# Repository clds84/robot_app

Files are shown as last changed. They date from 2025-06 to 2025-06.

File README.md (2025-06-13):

# Robot Project
<p align= "center" style="margin: 30px">
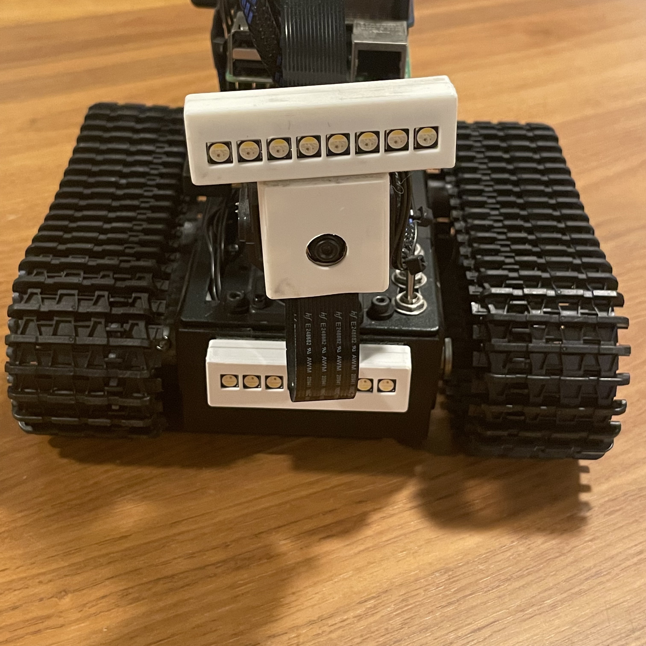
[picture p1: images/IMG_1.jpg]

</p>

This robot project is controlled via a client web interface served at `http://robot-hostname.local:8000` using WebSockets. Using a hostname instead of an IP address makes it easy to connect, even through a mobile hotspot, when configuring or troubleshooting WiFi in the field.

For my setup, the robot pairs with a dedicated **Mission Control** Pi that acts as a robot client app. It sends battery sensor readings (for its own display and the Pi) over sockets and opens the robot’s web interface in a browser for control via four rotary encoders and four key switches.

🔗 [Mission Control repo here](https://github.com/clds84/mission_control_app)

> A regular laptop or desktop can also be used as a client if you don’t want to build Mission Control hardware.

## 📑 Table of Contents

1. [Setup (Overview)](#-setup-overview)
2. [Features](#features)
3. [Hardware](#hardware)
4. [3D Printed Parts](#3d-printed-parts)
5. [How to Build](#how-to-build)
6. [System Overview](#system-overview)
7. [How to Use](#how-to-use)
8. [Dependencies](#-dependencies)
9. [Service Files](#service-files---copy-in-system-and-user-services)
10. [Powering On for Use](#powering-on-for-use)
11. [Operating robot in a new environment](#operating-robot-in-a-new-environment)
12. [Controls for Laptop or Desktop](#controls-for-laptop-or-desktop)
13. [Code](#code)
14. [Troubleshooting](#troubleshooting)

## 🔧 Setup (Overview)

This project involves physical hardware, system services, and network setup. Use this section as a high-level checklist to guide your deployment.

1. **Assemble hardware**  
  Wire up all components according to the parts list and included `.stl` files for 3D-printed mounts and protection.

2. **Flash Raspberry Pi OS and configure WiFi**  
  Set up the robot Pi headlessly using a mobile hotspot to enable SSH access and configure primary WiFi with `nmcli`.

3. **Clone this repo and set up the environment**
  ```bash
  git clone https://github.com/clds84/robot_app
  cd robot_app
  python3 -m venv venv
  source venv/bin/activate
  pip install -r requirements.txt
  ```
4. **Copy services**

    Copy `app.service, stream.service`, and `display_hat_stats.service` into `~/.config/systemd/user/` 
    Copy `neopixel.service` into `/etc/systemd/system/` (must run as root)
5. **Enable and start services**

    For user-level services:
    ```bash
    systemctl --user enable app.service stream.service display_hat_stats.service
    systemctl --user start app.service steam.service display_hat_stats.service
    ```
    For root-level service
    ```bash
    sudo systemctl enable neopixel.service
    sudo systemctl start neopixel.service
    ```
6. **Power on devices**

    Boot up both the robot Pi and the Mission Control Pi (if used).
7. **Access the robot interface**

    Open a browser and go to:
    `http://robot-hostname.local:8000`
8. **Operate the robot**

    Use key controls with a Mission Control, laptop, or desktop described below to drive motors, control motor speed, adjust servos, toggle LEDs and control brightness.

## Features

- WebSocket-based communication between robot and client
- Local web interface (`index.html`) served by the robot
- Integrated camera stream via `stream.py`
- Handles onboard logic for:
  - DC motors (4-wheel drive)
  - Pan/tilt servos for camera
  - NeoPixel LED sticks
- Emits battery sensor readings over sockets
- Receives sensor input (e.g., Mission Control battery levels) over sockets (if using Mission Control client)

## Hardware

- [Raspberry Pi 4]()
- [Adafruit DC Motor HAT]()
- [Adafruit Servo HAT]()
- [Pi Camera]()
- [Pan/tilt servo bracket]()
- [2 DC motors (one per side)]()
- [2 servo motors (for X and Y axes)]()
- [2 Adafruit NeoPixel sticks]()
- [2 Adafruit PowerBoost chargers (for Lithium Polymer (LiPo) battery)]()
- [2 Adafruit battery gauge monitors]()
- [Adafruit I2C multiplexer]()
- [Adafruit display HAT (for WiFi status and battery voltage)](https://www.adafruit.com/product/4393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)

## 3D Printed Parts

Included `.stl` files for:

- Camera housing  
- NeoPixel stick holders  
- Underbody chassis cover (motor protection)  

> **Note:** The underbody is a quick solution for protection. It can be a little tedious to remove/install but functional.

## How to Build

Please refer to the included photos for build guidance. Since chassis types may vary, I didn’t document the mechanical build step-by-step, but the photos will provide some insight. 

**Tips:**

- **Breadboard or loosely wire** all components first to test functionality before permanent mounting.
- Use a **jumper wire kit** and proper standoffs for organization and flexibility.
- You may need a **conical file** to widen mounting holes on the battery gauges or multiplexer to fit standoffs.
- The **display HAT** might seem redundant since battery data is also shown in the web interface, but it’s useful for checking battery level before/after shutdown, or confirming WiFi connection with a button press.
- **Power stacking**: The PowerBoost, battery gauges, and multiplexer stack cleanly using standoffs when aligned properly.

---

### Back Right 
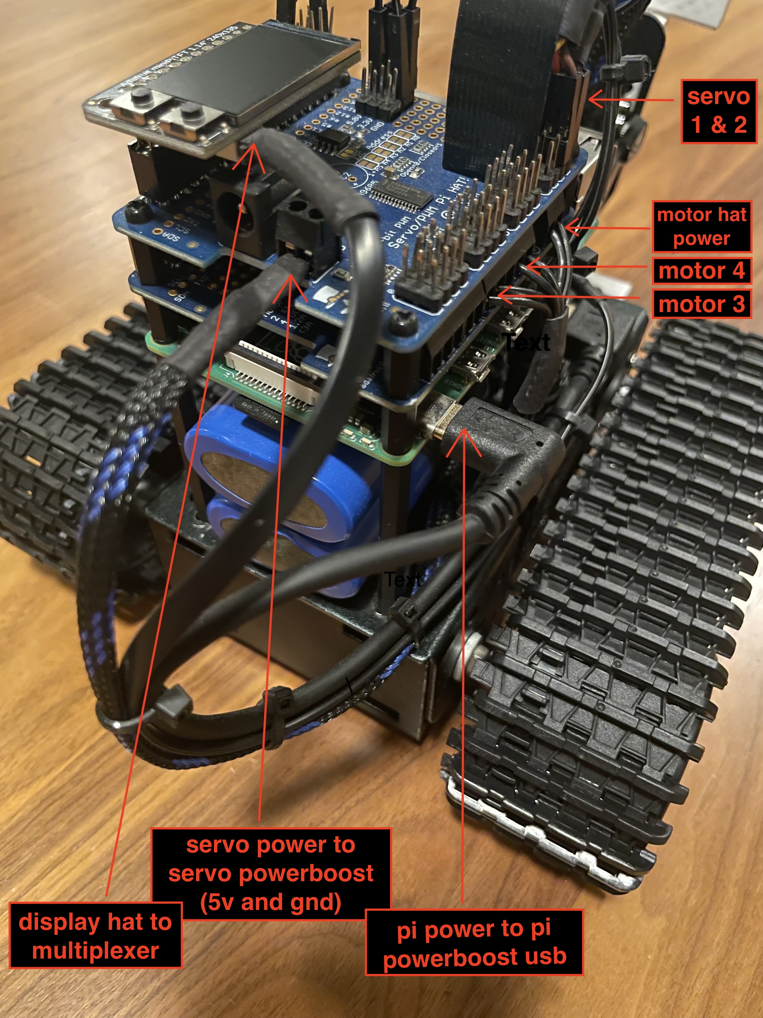
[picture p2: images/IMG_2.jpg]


This image shows the Display HAT stacked on the servo HAT, which is on top of the DC motor HAT, all mounted on the Raspberry Pi.  Other connection points for servo power, the display HAT, and the Pi power, are shown more clearly in later images. 

The six wires, two per DC motor, plus one for power and one for ground, run down straight down under the chassis. 

The **servo 1 & 2 wires** in the top right of the image come from the servo motors and are also shown more clearly in later images. The headers on this side of the servo HAT correspond to the 16-channel servo layout, and each row includes power, ground, and signal.

The camera ribbon runs through a slit in both the dc motor and servo HATs. 

---

### Multiplexer/Battery Gauge/Powerboost Stack
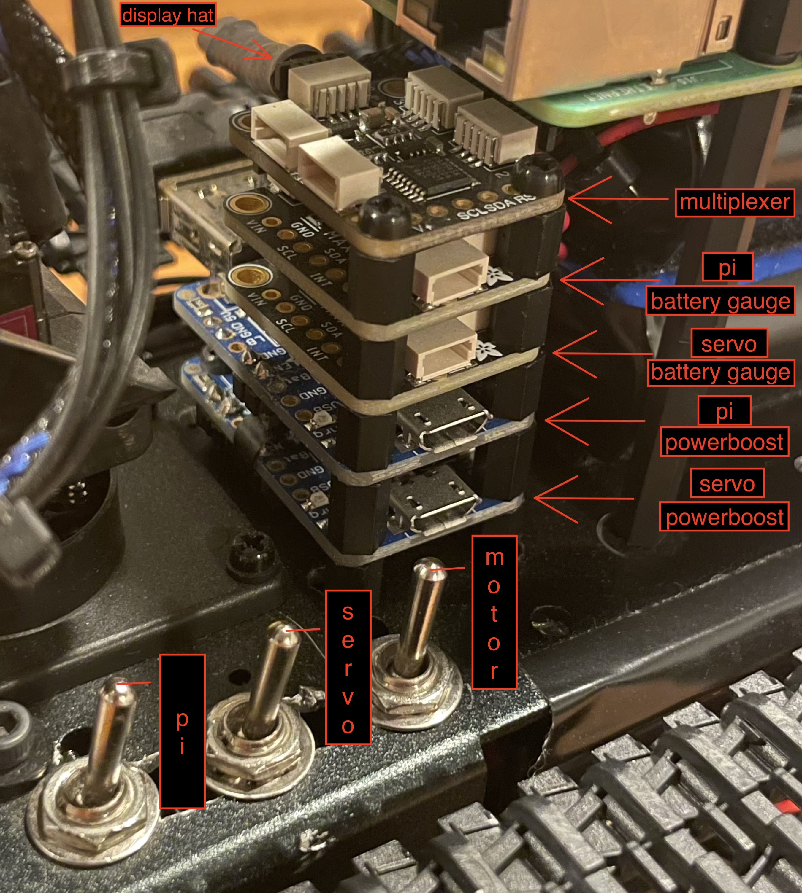
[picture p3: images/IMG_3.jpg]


This image shows:
  - Toggle switches for pi
  - Multiplexer
  - Battery gauges
  - Pi PowerBoost
  - Servo PowerBoost
  
  The power and ground wires for the DC motor ([motor wires](#back-right)) are connected to the motor toggle switch under the chassis. The toggle switches for the Pi and servo will be mentioned again.

---

### Top Left
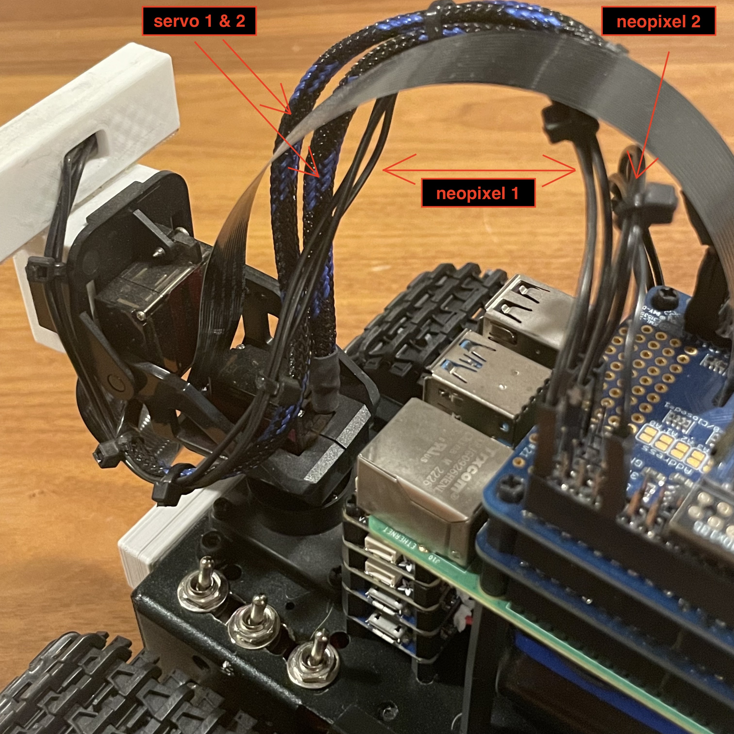
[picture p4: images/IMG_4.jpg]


The wires identified in this image are for:
  - NeoPixel 1 and 2 
  - Servo 1 and 2

Each Neopixel has a power, ground, and signal wire connected to the headesr on the servo HAT which correspond to the Pi's GPIO layout. The signal wire for NeoPixel 1 is connected to D21 and the one for NeoPixel 2 is connected to D12.

The wires for NeoPixel 2 will be mentioned again in a later image.

---
### Side View 
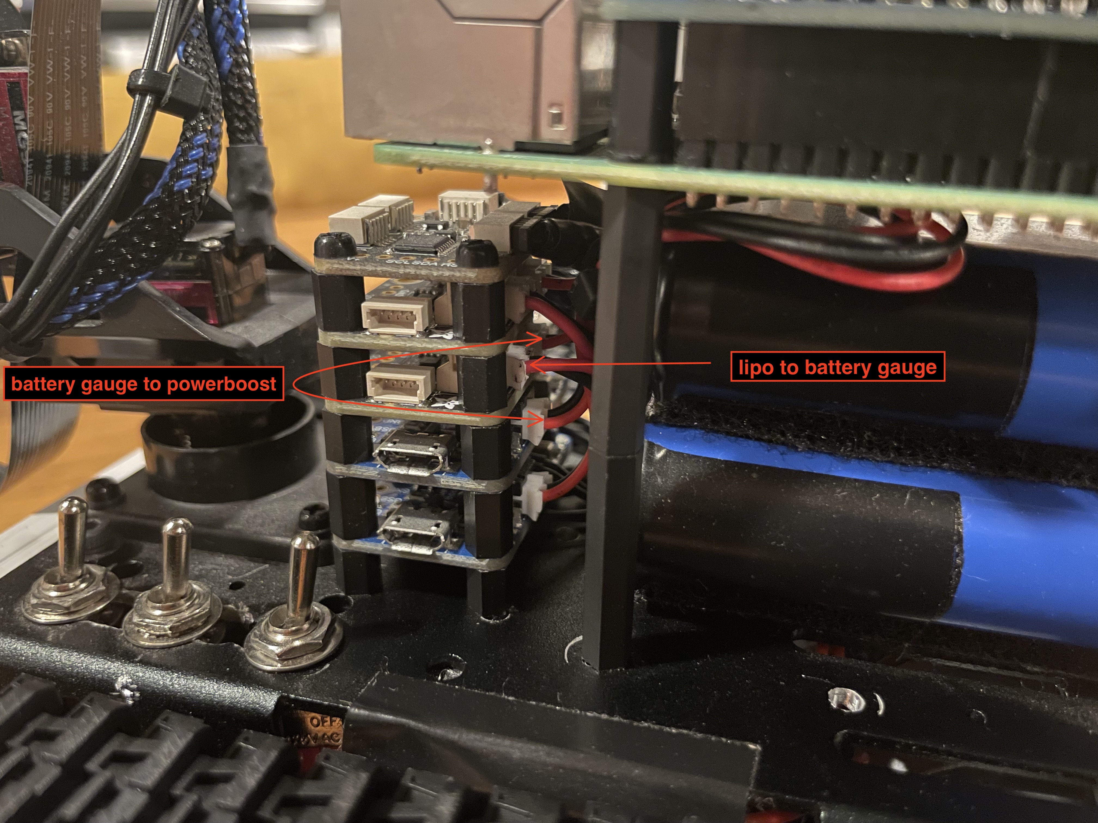
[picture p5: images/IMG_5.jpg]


Connect the LiPo JST connector to the battery gauge, then a JST cable from the battery gauge to the PowerBoost (these are the steps per battery gauge/PowerBoost combo).

---

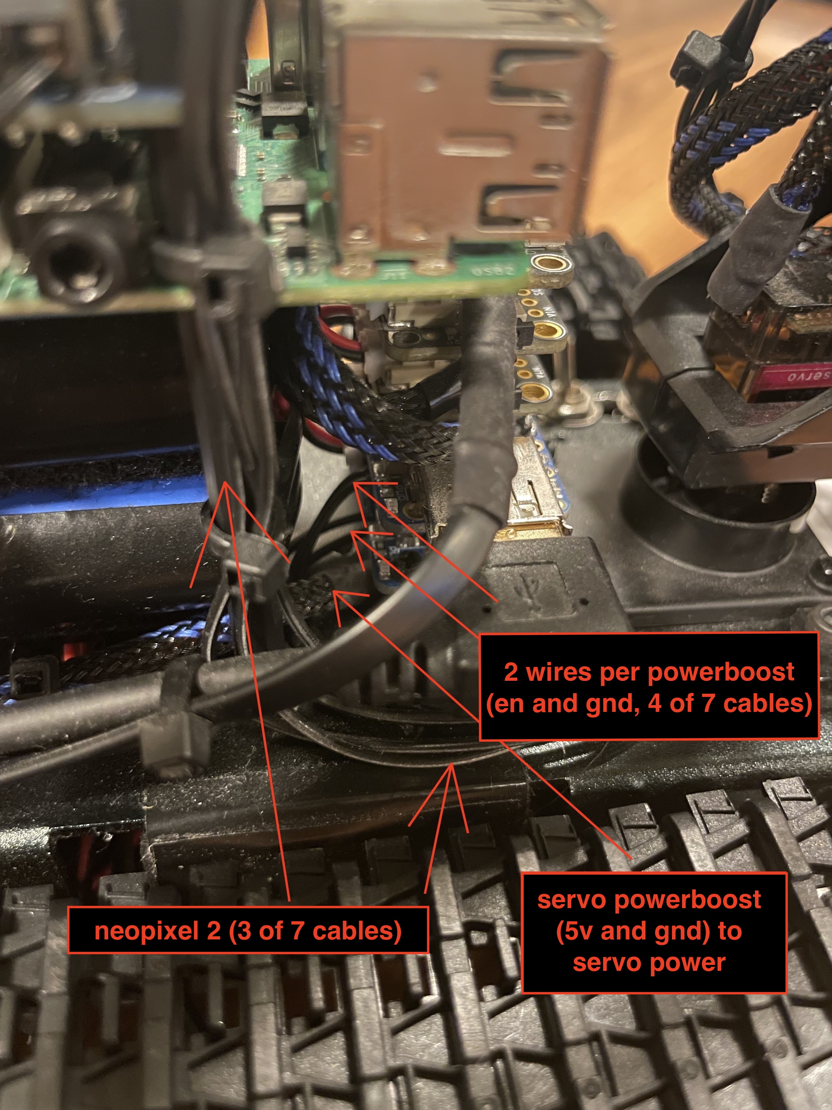
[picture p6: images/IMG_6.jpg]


Wires identified for:
  - Neopixel 2 [NeoPixel connection on HAT](#top-left)
  - Servo power ([Servo power](#back-right)) - use 5v and GND pins
  - PowerBoosts - use EN & GND pins

For aesthetic purposes, 90-degree headers are soldered to the bottom of each PowerBoost, facing inward toward the midline.

> **Note:** The EN and GND pins used for each PowerBoost (Pi and servo) run under the chassis and connect to the Pi and servo toggle switches. The difference between these and the motor switch is that the motor switch does not utilize a PowerBoost; instead, it enables power directly from the LiPo to the DC motor HAT, with no intermediary connections to be made. However, for the Pi and servo, the EN and GND will result in a LOW reading when the toggle switch is operated, and that will allow power from LiPo -> PowerBoost -> Pi/servo. The reason for doing this is to control the HIGH position when not using the robot and/or charging the LiPo batteries. If the toggle switch is in an OFF position, the PowerBoosts will not transfer voltage to the servo Hat or the Pi. However, the PowerBoosts will be operational for charging, via headers or the micro-usb port.

---

### Front Right
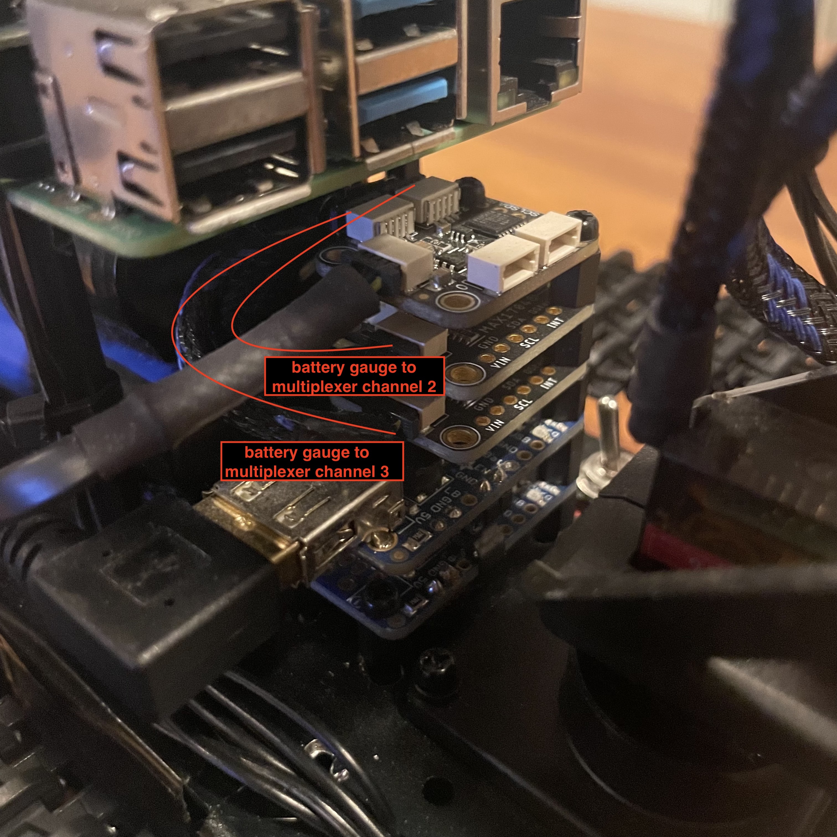
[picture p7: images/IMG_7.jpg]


Short QT Stemma connectors are used here to connect the battery gauges to the multiplexer. 

---

## System Overview

```text
[Mission Control Pi] --> [WebSocket] --> [Robot Pi]
       |                                     |
[Encoders + Keys]                    [Motors, Servos]
[Battery Gauges]                     [Camera + Stream]
                                     [NeoPixels, Battery Gauges]

--------------------------OR------------------------------------

[generic client] --> [WebSocket] --> [Robot Pi]
       |                                     |
    [Keys]                           [Motors, Servos]
                                     [Camera + Stream]
                                     [NeoPixels, Battery Gauges]
```

## How to Use

> See below for setting up WiFi if not using a wired connection and for operating robot in WiFi environments

### (Optional) Use a Virtual Environment

To avoid polluting your system Python, use the following in robot_app/:

```bash
cd robot_app
python3 -m venv venv
source venv/bin/activate
pip install -r requirements.txt
```

### 🧰 Dependenciess

#### 📎 **Dependencies to **Import** (Python Standard Library – no installation needed)**

These modules are part of Python 3 and do **not** require separate installation:

- `os`
- `sys`
- `time`
- `logging`
- `signal`
- `subprocess`
- `io`
- `threading`
- `atexit`
- `socketserver`
- `http.server`
- `Condition` (from `threading`)

> These modules are included with any modern Python 3 installation.

### 📦 Dependencies to **Install** (Third-Party Packages)

This project requires the following main Python packages, which are included in the requirements.txt file:

- `flask`
- `flask_socketio`
- `Pillow` (for image manipulation, imported as `PIL`)
- `adafruit-blinka`
- `adafruit-circuitpython-motorkit`
- `adafruit-circuitpython-servokit`
- `adafruit-circuitpython-max1704x`
- `adafruit-circuitpython-tca9548a`
- `adafruit-circuitpython-rgb-display`
- `adafruit-circuitpython-neopixel`
- `picamera2` (may require additional OS-level setup)

You can install these dependencies with:

```bash
pip install -r requirements.txt
```

### Service Files - copy in system and user services

`app.service, stream.service`, and `display_hat_stats.service` should be copied in `~/.config/systemd/user/`, however `neopixel.service` should be installed in `/etc/systemd/system/`because it has to be run as root. 

> Run `update_service.sh` to copy the latest versions of all service files from this repo into the correct system/user directories.

### Powering On for Use

- Once the above steps have been completed, the robot Pi automatically runs `app.py` and `stream.py` web interface at `http://robot-hostname.local:8000` through user services. `neopixel_setup.py` runs as a separate service at root level as root privileges are required for it to work. **Note:** Do not name your file `neopixel.py` or it will conflict with the Adafruit NeoPixel module.
- SSH can be used to troubleshoot and is used to shutdown devices. Termius is a good mobile app for communication if out in the field. 

### Operating robot in a new environment

- first step after boot is to setup WiFi. If running headless:
  - Use mobile hotspot when flashing OS that will serve as a temporary SSH session when in the field in order to setup the primary WiFi in that environment.
  - Make use of WiFi script including `nmcli` commands. 
  - Once the WiFi script has been used, adjust WiFi priority value with `nmcli connection modify <connection_name> connection.autoconnect-priority: <number>` (**Note:** higher value means higher priority. This will avoid hiccups if the hotspot is still on and has a higher priority than the new WiFi connection.) 

After WiFi setup, the web interface will be properly served and `http://robot-hostname.local:8000` will include the stream from `stream.py` and the battery gauge readings from the robot and Mission Control (if applicable) broadcast via WebSockets. The User Interface (UI) is designed primarily for Mission Control's 7" display, so it might feel light on a laptop or desktop. There is room for improving those use cases if preferred over Mission Control, including click events as an alternative to key down/up events. 

### Controls for Laptop or Desktop

> **Note:** Mission Control uses rotary encoders for all key down/up functionality below, except for the WASD keyboard layout for Forward-Left-Backward-Right, which follows an ortho-linear QWERTY layout. 

The interface is minimal because Mission Control uses physical rotary encoders, not on-screen controls.

#### Motor Movement
- <kbd>W</kbd> – Move robot forward
- <kbd>A</kbd> – Turn robot left
- <kbd>S</kbd> – Move robot in reverse
- <kbd>D</kbd> – Turn robot right
- <kbd>W</kbd> – Move robot forward

#### Camera Movement
- <kbd>J</kbd> – Rotate camera left
- <kbd>L</kbd> – Rotate camera right
- <kbd>I</kbd> – Tilt camera up
- <kbd>K</kbd> – Tilt camera down
- <kbd>N</kbd> – Reset camera to center position.

#### LED Control
- <kbd>Z</kbd> – Toggle LED strip
- <kbd>X</kbd> - Decrease LED strip brightness
- <kbd>C</kbd> - Increase LED strip brightness

#### Speed Control
- <kbd>F</kbd> – Toggle motor speed range
- <kbd>G</kbd> - Decrease motor speed
- <kbd>H</kbd> - Increase motor speed

### Code

- The Logic for interpreting control inputs and sending data is located in `app.py`.

- Sensor readings from Mission Control’s battery gauges are sent to the robot in real-time via WebSocket. To avoid errors when a Mission Control client is not used, there is a conditional check in `templates/index.html`:

```
// Battery reading from Mission Control
socket.on('battery_update_mc', (data) => {
    const mcEl = document.getElementById('battery-status-mc')
    if (mcEl) {
        mcEl.innerHTML = data.battery;
        console.log("Got mision control update:", data);
    }
});
```

- Depending on your use case, you may want to adjust the camera resolution (`width` x `height` in `picam2.configure(...)`) and the `<img>` element dimensions in the HTML (`width`x `height` attributes) accordingly.

- For debugging or to check events in realtime, use app.log and neopixel.log that will be created in `robot_app/logs/` when services run. Make sure to uncomment lines such as: `logger.info('Current motor speeds: %s, %s', motor3Speed, motor4Speed)`

### Troubleshooting

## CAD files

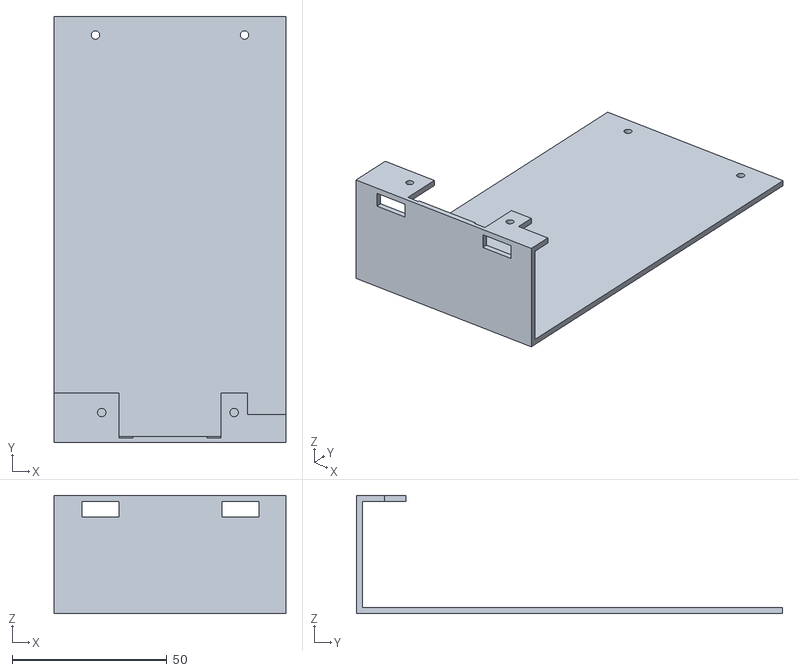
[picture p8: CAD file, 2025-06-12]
stl_files/undercarriage_front_and_bottom.stl
75.0 x 137.8 x 38.3

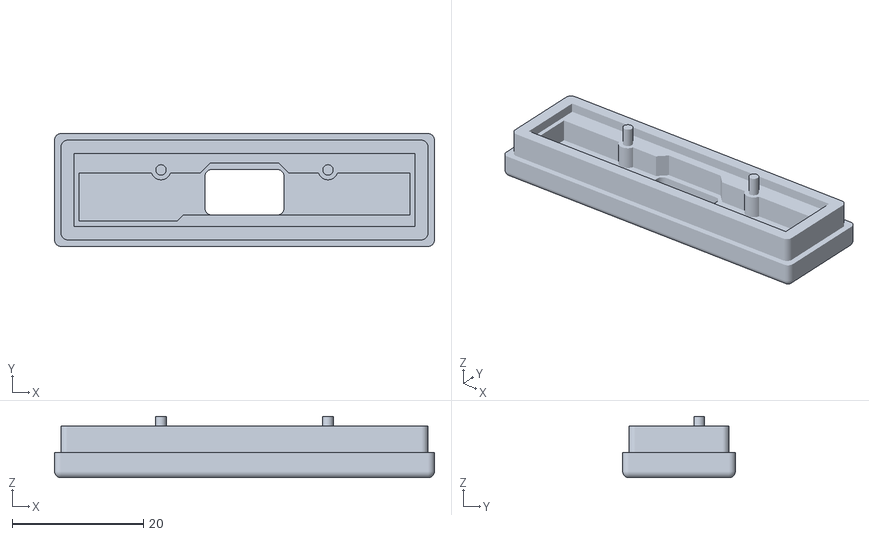
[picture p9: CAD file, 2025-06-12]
stl_files/neopixel_case_back.stl
57.8 x 17.2 x 9.35

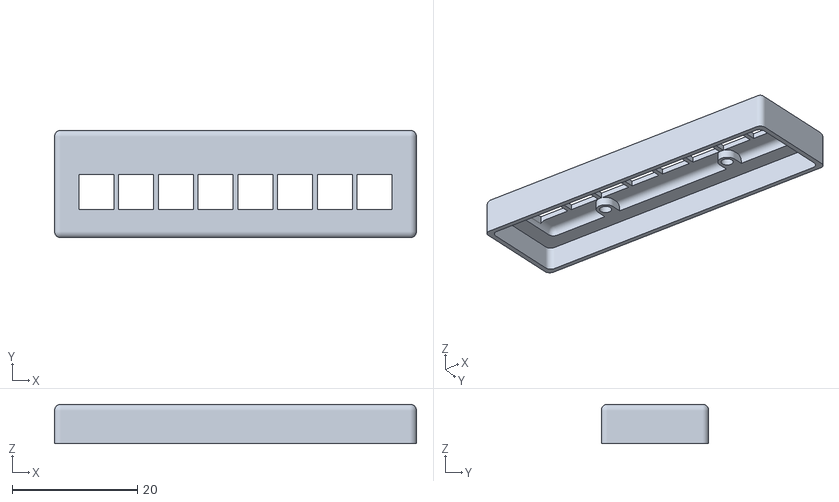
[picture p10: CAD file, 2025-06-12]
stl_files/neopixel_case_front.stl
57.8 x 17.2 x 6.30

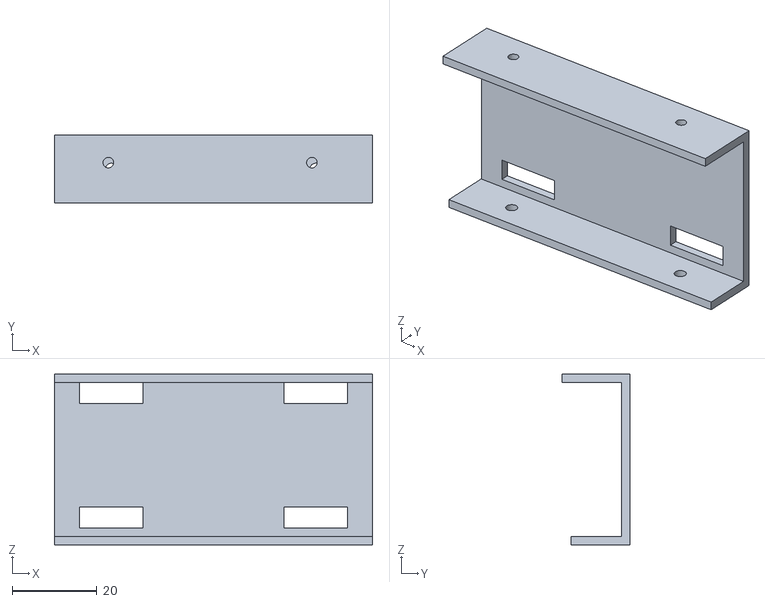
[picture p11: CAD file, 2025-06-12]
stl_files/undercarriage_back.stl
75.0 x 16.0 x 40.3

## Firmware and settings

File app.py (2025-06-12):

import os
import board
import threading
import logging
from flask import Flask, render_template, request
from flask_socketio import SocketIO, emit
from adafruit_motorkit import MotorKit
from adafruit_servokit import ServoKit
import adafruit_max1704x
import adafruit_tca9548a

# ========== Hardware Initialization ==========

# Shared I2C bus
i2c = board.I2C()

# Initialize multiplexer over I2C
pca = adafruit_tca9548a.TCA9548A(i2c)

# Initialize battery fuel gauges on multiplexer channels 2 and 3
piBat = adafruit_max1704x.MAX17048(pca[3])
servoBat = adafruit_max1704x.MAX17048(pca[2])

# Initialize servo motors on Servo/Motor HAT over I2C
kitServo = ServoKit(channels=16)

# Initial angle values for servos
movement0 = 90
movement1 = 90
kitServo.servo[14].angle = movement0
kitServo.servo[15].angle = movement1

# Initialize DC motors on Servo/Motor HAT (shared I2C bus)
kit = MotorKit(i2c=i2c)
motor3Speed = 1.0
motor4Speed = 1.0
motor_button_pressed = False

motor_lock = threading.Lock()

# Set up logging to file for troubleshooting
log_dir = 'logs'
os.makedirs(log_dir, exist_ok=True)
log_file = os.path.join(log_dir, 'app.log')
print("Log file will be written to:", log_file)

logging.basicConfig(
    filename=log_file, 
    level=logging.INFO,
    format='%(asctime)s [%(levelname)s] %(message)s',
    force=True
)

logger = logging.getLogger(__name__)

logger.info('Current motor speeds: %s, %s', motor3Speed, motor4Speed)

app = Flask(__name__)
socketio = SocketIO(app, cors_allowed_origins="*")

# Store latest battery data globally
robot_battery_data = {"battery": "<span class='purple'>Waiting for battery data...</span>"}

# Handle client connection
@socketio.on('connect')
def handle_connect():
    print("Client connected:", request.sid)
    emit('battery_update', robot_battery_data)  

# Handle client disconnection
@socketio.on('disconnect')
def handle_disconnect():
    print("Client disconnected:", request.sid)

# Listen for battery updates broadcasted by Mission Control and relayed via the server
@socketio.on('battery_update_mc')
def handle_battery_update_mc(data):
    print("Received battery_update_mc:", data)
    socketio.emit('battery_update_mc', data, skip_sid=request.sid)

def get_battery_life():
    # Determine text color based on battery percentage
    if piBat.cell_percent > 50:
        pi_font_color = 'neon'
    elif 20 < piBat.cell_percent < 50:
        pi_font_color = 'yellow'
    else:
        pi_font_color = 'red'

    if servoBat.cell_percent > 50:
        servo_font_color = 'neon'
    elif 20 < servoBat.cell_percent < 50:
        servo_font_color = 'yellow'
    else:
        servo_font_color = 'red'

    # Format battery status message as HTML with color-coded values
    return {
        "battery": (
            "<span class='amber'>ROBOT </span>"
            "PI "
            f"<span class='{pi_font_color}'>{piBat.cell_percent:.1f}%</span> / "
            f"<span class='{pi_font_color}'>{piBat.cell_voltage:.2f}V</span> "
            "SERVO "
            f"<span class='{servo_font_color}'>{servoBat.cell_percent:.1f}%</span> / "
            f"<span class='{servo_font_color}'>{servoBat.cell_voltage:.2f}V</span>"
        )
    }

def battery_life_thread():
    global robot_battery_data 
    while True:
        robot_battery_data = get_battery_life()
        socketio.emit('battery_update', robot_battery_data)
        socketio.sleep(1)

socketio.start_background_task(battery_life_thread)

@app.route('/')
def index():
    return render_template('index.html')

# Handle incoming commands to control motors and servos
@socketio.on('command')
def handle_command(command):
    global movement0, movement1, motor3Speed, motor4Speed, motor_button_pressed
    with motor_lock:
        logger.info(f"Received command: {command}")

        # --- Robot Movement Commands ---
        if command == 'forward':
            kit.motor3.throttle = 0.929
            kit.motor4.throttle = -1.0
        elif command == 'reverse':
            kit.motor3.throttle = -motor3Speed
            kit.motor4.throttle = motor4Speed
        elif command == 'left':
            kit.motor3.throttle = -1.0
            kit.motor4.throttle = -1.0
        elif command == 'right':
            kit.motor3.throttle = 1.0
            kit.motor4.throttle = 1.0
        elif command == 'stop':
            kit.motor3.throttle = 0
            kit.motor4.throttle = 0

        # --- Robot Speed Control ---
       
        elif command == 'motorSpeedDefault':
            if motor_button_pressed == False:
                motor_button_pressed = True
                motor3Speed = 1.0
                motor4Speed = 1.0
                # Uncomment to troubleshoot
                # logger.info('Current motor speeds: %s, %s', motor3Speed, motor4Speed)
            elif motor_button_pressed == True:
                motor_button_pressed = False 
                motor3Speed = motor3Speed
                motor4Speed = motor4Speed
                # Uncomment to troubleshoot
                # logger.info('Current motor speeds: %s, %s', motor3Speed, motor4Speed)
        elif command == 'motorSpeedIncrease':
            motor3Speed = min(1.0, motor3Speed + 0.025)
            motor4Speed = min(1.0, motor4Speed + 0.025)
            # Uncomment to troubleshoot
            # logger.info('Current motor speeds: %s, %s', motor3Speed, motor4Speed)
        elif command == 'motorSpeedDecrease':
            motor3Speed = max(.75, motor3Speed - 0.025)
            motor4Speed = max(.75, motor4Speed - 0.025)
            # Uncomment to troubleshoot
            # logger.info('Current motor speeds: %s, %s', motor3Speed, motor4Speed)
        # Servo (camera) commands
        elif command == 'cameraLeft':
            if movement1 < 138:
                movement1 += 8
                kitServo.servo[15].angle = movement1
        elif command == 'cameraRight':
            if movement1 > 30:
                movement1 -= 8
                kitServo.servo[15].angle = movement1
        elif command == 'cameraUp':
            if movement0 > 30:
                movement0 -= 10
                kitServo.servo[14].angle = movement0
        elif command == 'cameraDown':
            if movement0 < 120:
                movement0 += 10
                kitServo.servo[14].angle = movement0
        elif command == 'cameraCenter':
            movement0 = 90
            movement1 = 90
            kitServo.servo[14].angle = movement0
            kitServo.servo[15].angle = movement1

        else:
            logger.warning(f"Unknown command: {command}")

    emit('status', {'status': 'ok', 'command': command})

if __name__ == '__main__':
    socketio.run(app, host='0.0.0.0', port=8000)

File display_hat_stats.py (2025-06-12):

# SPDX-FileCopyrightText: 2021 ladyada for Adafruit Industries
# SPDX-License-Identifier: MIT
# Modified by clds84, 2025

# -*- coding: utf-8 -*-

import time
import subprocess
import digitalio
import board
from PIL import Image, ImageDraw, ImageFont
from adafruit_rgb_display import st7789
import adafruit_max1704x
import adafruit_tca9548a
import atexit
import signal
import sys

# Shared I2C bus
i2c = board.I2C()  

# Initialize multiplexer over I2C
pca = adafruit_tca9548a.TCA9548A(i2c)

# Initialize battery fuel gauges on multiplexer channels 2 and 3
piBat = adafruit_max1704x.MAX17048(pca[3])
servoBat = adafruit_max1704x.MAX17048(pca[2])

# Configuration for CS and DC pins (these are FeatherWing defaults on M0/M4):
cs_pin = digitalio.DigitalInOut(board.CE0)
dc_pin = digitalio.DigitalInOut(board.D25)
reset_pin = None

# Config for display baudrate (default max is 24mhz):
BAUDRATE = 64000000

# Setup SPI bus using hardware SPI:
spi = board.SPI()

# Create the ST7789 display:
disp = st7789.ST7789(
    spi,
    cs=cs_pin,
    dc=dc_pin,
    rst=reset_pin,
    baudrate=BAUDRATE,
    width=135,
    height=240,
    x_offset=53,
    y_offset=40,
)

# Setup button hardware
buttonA = digitalio.DigitalInOut(board.D23)
buttonB = digitalio.DigitalInOut(board.D24)
buttonA.switch_to_input()
buttonB.switch_to_input()
# buttonA.switch_to_input(pull=digitalio.Pull.UP)
# buttonB.switch_to_input(pull=digitalio.Pull.UP)

# Create blank image for drawing.
# Make sure to create image with mode 'RGB' for full color.
height = disp.width  # we swap height/width to rotate it to landscape!
width = disp.height
image = Image.new("RGB", (width, height))
rotation = 270

# Get drawing object to draw on image.
draw = ImageDraw.Draw(image)

# Draw a black filled box to clear the image.
draw.rectangle((0, 0, width, height), outline=0, fill=(0, 0, 0))
disp.image(image, rotation)

# Draw some shapes.
# First define some constants to allow easy resizing of shapes.
padding = -2
top = padding
bottom = height - padding
# Move left to right keeping track of the current x position for drawing shapes.
x = 0

# Alternatively load a TTF font.  Make sure the .ttf font file is in the
# same directory as the python script!
# Some other nice fonts to try: http://www.dafont.com/bitmap.php
font = ImageFont.truetype("/usr/share/fonts/truetype/dejavu/DejaVuSans.ttf", 24)
readings_font = ImageFont.truetype("/usr/share/fonts/truetype/dejavu/DejaVuSans.ttf", 25) 
ssid_font = ImageFont.truetype("/usr/share/fonts/truetype/dejavu/DejaVuSans.ttf", 22) 
device_font = ImageFont.truetype("/usr/share/fonts/truetype/dejavu/DejaVuSans.ttf", 28)  

# Turn on the backlight
backlight = digitalio.DigitalInOut(board.D22)
backlight.switch_to_output()
#use False if using buttons, so we start with backlight off
backlight.value = True

def cleanup():
    backlight.value = False

def handle_sigterm(signum, frame):
    cleanup()
    sys.exit(0)

atexit.register(cleanup)
signal.signal(signal.SIGTERM, handle_sigterm)
signal.signal(signal.SIGINT, handle_sigterm)  # also handle Ctrl+C gracefully

while True:
    try:
        # Draw a black filled box to clear the image.
        draw.rectangle((0, 0, width, height), outline=0, fill=0)

        # =========================== Shell scripts for system monitoring from here: ============================
        # https://unix.stackexchange.com/questions/119126/command-to-display-memory-usage-disk-usage-and-cpu-load

        # For pressing B
        cmd = "hostname -I | cut -d' ' -f1"
        IP = "IP: " + subprocess.check_output(cmd, shell=True).decode("utf-8")
        cmd = "hostname"
        Hostname = "Host: " + subprocess.check_output(cmd, shell=True).decode("utf-8")
        cmd = "iwgetid wlan0 -r"
        SSID = "SSID: " + subprocess.check_output(cmd, shell=True).decode("utf-8")   
        # =======================================================================================================
        
        # for buttonB.value and buttonA.value (display without pressing A or B)
        battery_line_1 = "      Pi       Servo"
        battery_line_2 = f"V:  {piBat.cell_voltage:.2f}v    {servoBat.cell_voltage:.2f}v"    
        battery_line_3 = f"C:  {piBat.cell_percent:.1f}%   {servoBat.cell_percent:.1f}%" 
        battery_line_4 = f"D: {piBat.charge_rate:.1f}%    {servoBat.charge_rate:.1f}%"
        
        if buttonB.value and buttonA.value:
            draw.rectangle((0, 0, width, height), outline=0, fill=0)
            y = top
            draw.text((x, y), battery_line_1, font=device_font, fill="#00FF00")
            y += font.getsize(battery_line_1)[1]
            y += 20  
            draw.text((x, y), battery_line_2, font=readings_font, fill="#00FF00")
            y += font.getsize(battery_line_2)[1]
            draw.text((x, y), battery_line_3, font=readings_font, fill="#00FF00")
            y += font.getsize(battery_line_3)[1]
            draw.text((x, y), battery_line_4, font=readings_font, fill="#00FF00")
            y += font.getsize(battery_line_4)[1]
            disp.image(image, rotation)
            time.sleep(0.1)
        if buttonA.value and not buttonB.value: #button A pressed and display toggled on/off
            if backlight.value == True:
                backlight.value = False
                time.sleep(.5)
            elif backlight.value == False:
                backlight.value = True
                time.sleep(.5)
        if buttonB.value and not buttonA.value: #button B pressed and IP/Hostname/SSID toggled on/off
            draw.rectangle((0, 0, width, height), outline=0, fill=0)
            y = top
            draw.text((x, y), IP, font=font, fill="#FFFFFF")
            y += font.getsize(IP)[1]
            draw.text((x, y), Hostname, font=font, fill="#FF00FF")
            y += font.getsize(Hostname)[1]
            draw.text((x, y), SSID, font=ssid_font, fill="#FF4051")
            disp.image(image, rotation)
            time.sleep(0.1)
    except KeyboardInterrupt:
        cleanup()
        sys.exit(0)

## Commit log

2025-06-07 fix body/image styling, add css for stream and font colors for battery gauge readings,Add client handlers for battery updates from robot and mission control broadcasts
2025-06-12 clean up formatting, remove logs, refactor motorspeed key down event listeners, and add browser reload logic in case mission control is on before robot"
2025-06-12 Add battery gauges (transmit readings via WebSockets), use logging for troubleshooting, and add motorspeed conditional statements for changing motor speed of dc motors
2025-06-12 add .stl files
    [neopixel_case_back.stl, neopixel_case_front.stl, undercarriage_back.stl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]
2025-06-12 remove print(), uncomment and add troubleshoot instruction comment for logger, add format and force for logging object and add neopixel-specific log file
2025-06-12 move stl files into folder for better organization
    [neopixel_case_back.stl, neopixel_case_front.stl, undercarriage_back.stl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]
2025-06-12 moved files into stl and services directories for better organization
    [neopixel_case_back.stl, neopixel_case_front.stl, undercarriage_back.stl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]
